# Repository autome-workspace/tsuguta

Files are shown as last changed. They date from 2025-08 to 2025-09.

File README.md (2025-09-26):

# tsugutaのリポジトリ

## KiCadファイル
- MD-AM2837
  - AM2837を使ったシンプルなモタドラ。定格13.5V3.5A(peak 6A)。絶対最大定格15V
- MD-IR2302
  - IR2302を使ったモタドラ。FETにはTOSHIBA製TK7R4A10PL(絶対最大定格100V50A)を使用予定。
- lipo-S.V.-simple-v2
  - li-poバッテリー用の電源電圧監視・保護回路第2版。定格24V35A。各セルの電圧は監視していないため、ほんとは良くない。あくまで簡易版
- my-lib
  - 作る価値のある部品だけ
   
## 【試験運用中】tagについて
- v.x.y
  - x: 0は試作中で動作保証なし、1以降は動く物。1以降では物理的・プログラム的に重大な変更(コネクタ変更、真理値表変更)の場合などに上げる。
  - y: 小さな変更の場合はこちらを上げていく。

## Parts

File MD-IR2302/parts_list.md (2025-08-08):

リファレンス|値|数量|リンク|備考
---|---|---|---|---
C1,C3|10uF|2|[秋月](https://akizukidenshi.com/catalog/g/g113336/)|
C2,C5,C6,C7,C9|0.1uF|5|[秋月](https://akizukidenshi.com/catalog/g/g111384/)|
C4|470uF|1|[秋月](https://akizukidenshi.com/catalog/g/g102719/)|
C8|0.47uF|1|[秋月](https://akizukidenshi.com/catalog/g/g117142/)|
C10,C11|220uF|2|[秋月](https://akizukidenshi.com/catalog/g/g102718/)|実装しない
D1,D2|1N4148|2|[秋月](https://akizukidenshi.com/catalog/g/g100941/)|
J1|XT60メス基板実装用|1|[秋月](https://akizukidenshi.com/catalog/g/g118155/)|
J2|XH3ピン|1|[秋月](https://akizukidenshi.com/catalog/g/g112248/)|
J3,J4|XH2ピン|2|[秋月](https://akizukidenshi.com/catalog/g/g112247/)|実装しない
J5|XT60オス基板実装用|1|[秋月](https://akizukidenshi.com/catalog/g/g118156/)|
LDO1|NJM7805|1|[秋月](https://akizukidenshi.com/catalog/g/g111237/)|
Q1,Q2,Q3,Q4|TK7R4A10PL|4|[秋月](https://akizukidenshi.com/catalog/g/g116488/)|
R1,R2,R3,R4|47kΩ|4|千石地下一階にて入手可能|1608サイズ
R5,R6|910Ω|2|千石地下一階にて入手可能|1608サイズ
R7,R8,R9,R10|4.7Ω|4|千石地下一階にて入手可能|1608サイズ、抵抗ない時はショートでも可
U1,U2|IR2302|2|[秋月](https://akizukidenshi.com/catalog/g/g115656/)|
U3,U4|TLP2361|2|[秋月](https://akizukidenshi.com/catalog/g/g111004/)|

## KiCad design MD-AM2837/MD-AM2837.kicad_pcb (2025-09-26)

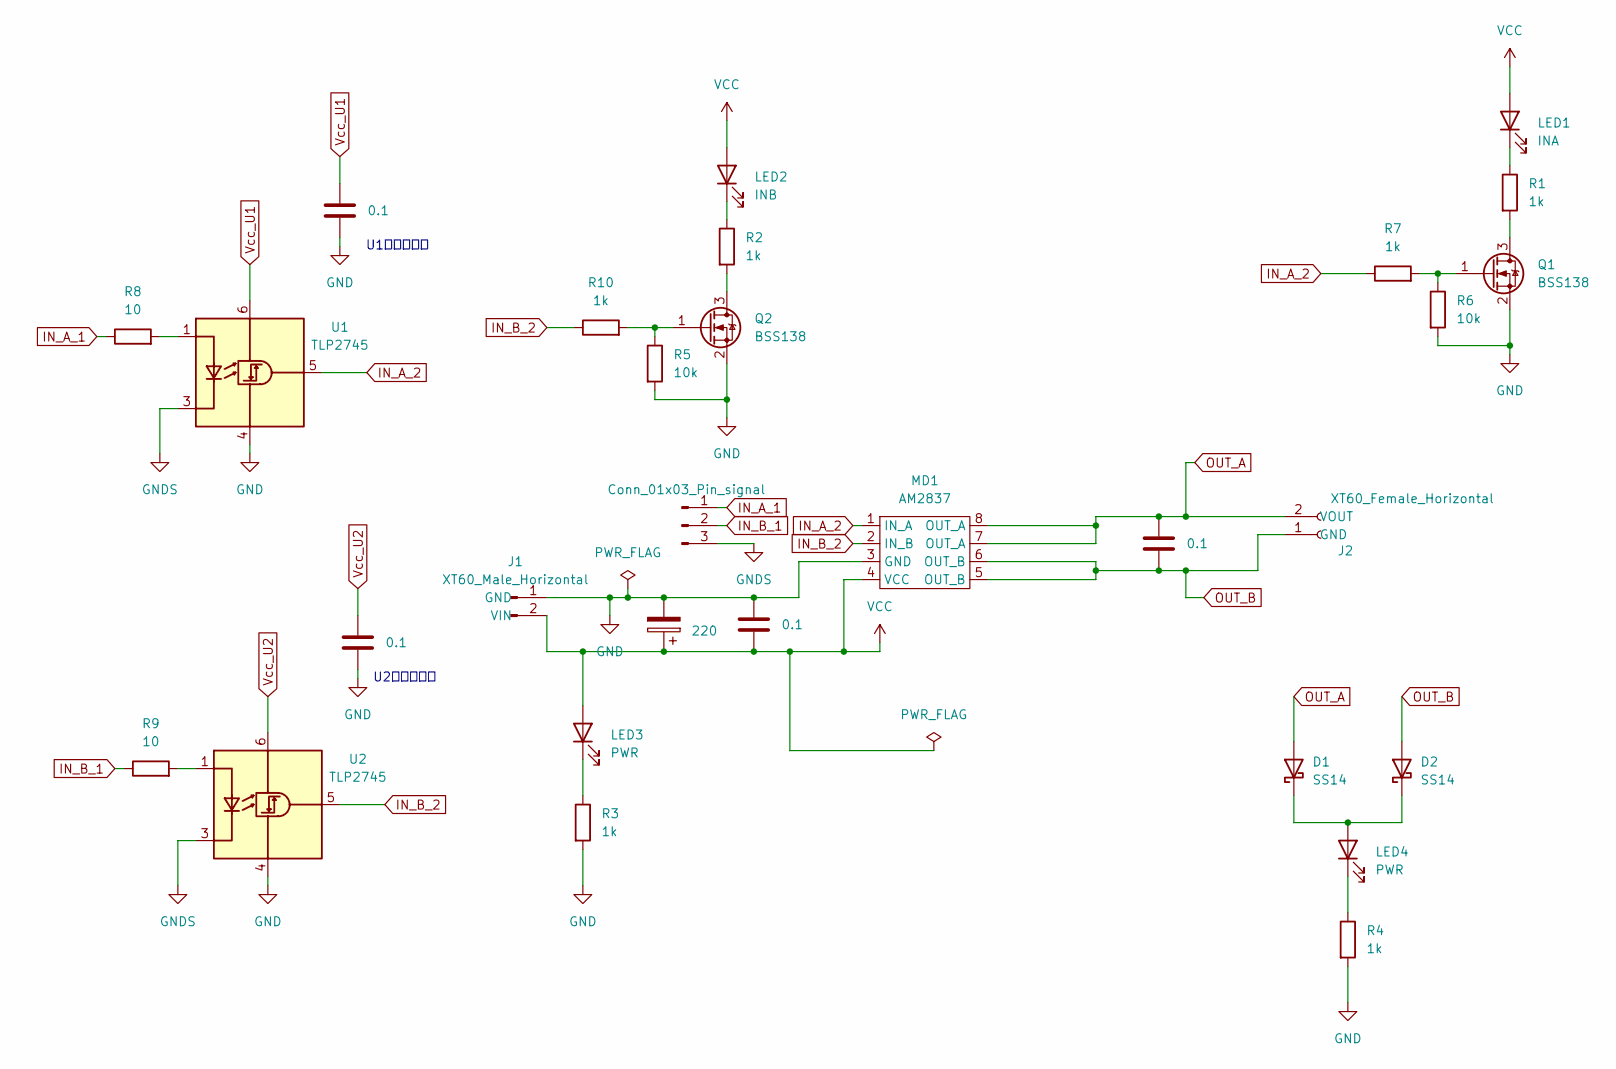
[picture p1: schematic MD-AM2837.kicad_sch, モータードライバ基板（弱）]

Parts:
C1: 220; C_Radial_D8.0mm_H11.5mm_P3.50mm
C2, C3, C4, C5: 0.1; C_0603_1608Metric_Pad1.08x0.95mm_HandSolder
D1, D2: SS14; D_SMA
J1: XT60_Male_Horizontal; AMASS_XT60PW-M_1x02_P7.20mm_Horizontal
J2: XT60_Female_Horizontal; AMASS_XT60PW-F_1x02_P7.20mm_Horizontal
J3: Conn_01x03_Pin_signal; JST_XH_B3B-XH-A_1x03_P2.50mm_Vertical
LED1: INA; LED_0603_1608Metric_Pad1.05x0.95mm_HandSolder
LED2: INB; LED_0603_1608Metric_Pad1.05x0.95mm_HandSolder
LED3, LED4: PWR; LED_0603_1608Metric_Pad1.05x0.95mm_HandSolder
MD1: AM2837; SOP-8_3.9x4.9mm_P1.27mm
Q1, Q2: BSS138; SOT-23
R1, R2, R3, R4, R7, R10: 1k; R_0603_1608Metric_Pad0.98x0.95mm_HandSolder
R5, R6: 10k; R_0603_1608Metric_Pad0.98x0.95mm_HandSolder
R8, R9: 10; R_0603_1608Metric_Pad0.98x0.95mm_HandSolder
U1, U2: TLP2745; SO-6L_10x3.84mm_P1.27mm

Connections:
GND: C1.2, C2.1, C4.2, C5.2, J1.1 (GND), MD1.3 (GND), Q1.2 (S), Q2.2 (S), R3.2, R4.2, R5.2, R6.2, U1.4 (GND), U2.4 (GND)
GNDS: J3.3, U1.3 (K), U2.3 (K)
IN_A_1: J3.1, R8.1
IN_A_2: MD1.1 (IN_A), R7.1, U1.5 (VO)
IN_B_1: J3.2, R9.1
IN_B_2: MD1.2 (IN_B), R10.1, U2.5 (VO)
unnamed: D1.1 (K), D2.1 (K), LED4.2 (A)
unnamed: LED1.1 (K), R1.1
unnamed: LED2.1 (K), R2.1
unnamed: LED3.1 (K), R3.1
unnamed: LED4.1 (K), R4.1
unnamed: Q1.3 (D), R1.2
unnamed: Q1.1 (G), R6.1, R7.2
unnamed: Q2.3 (D), R2.2
unnamed: Q2.1 (G), R5.1, R10.2
unnamed: R8.2, U1.1 (A)
unnamed: R9.2, U2.1 (A)
OUT_A: C3.1, D1.2 (A), J2.2 (VOUT), MD1.7 (OUT_A), MD1.8 (OUT_A)
OUT_B: C3.2, D2.2 (A), J2.1 (GND), MD1.5 (OUT_B), MD1.6 (OUT_B)
VCC: C1.1, C2.2, J1.2 (VIN), LED1.2 (A), LED2.2 (A), LED3.2 (A), MD1.4 (VCC)
Vcc_U1: C4.1, U1.6 (VDD)
Vcc_U2: C5.1, U2.6 (VDD)

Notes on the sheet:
U1に近づける
U2に近づける

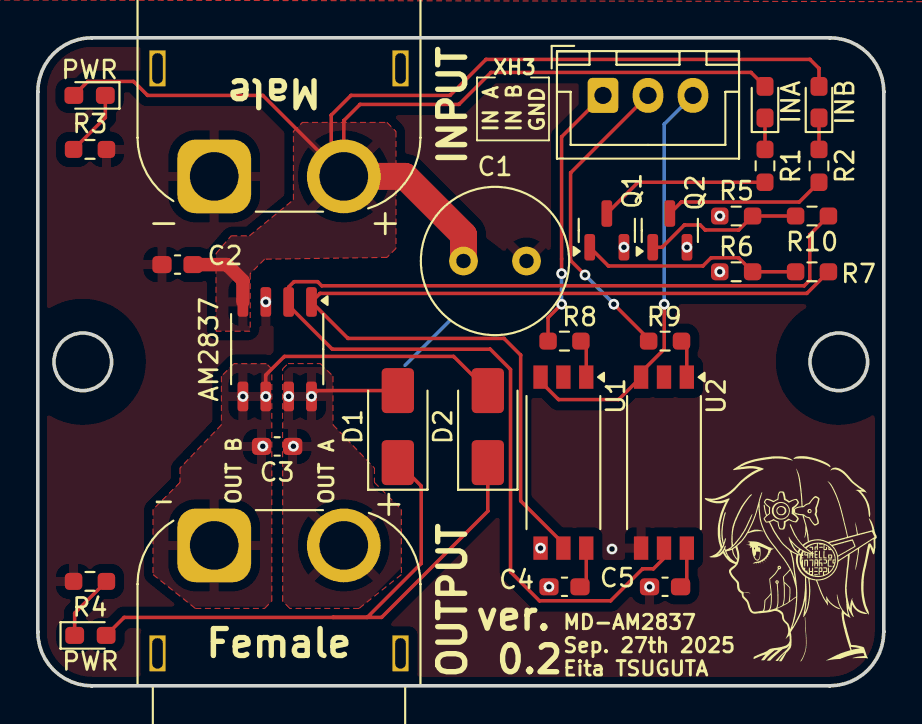
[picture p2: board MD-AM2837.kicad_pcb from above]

Board: 2 copper layers, 47.0 x 36.0 mm, 29 parts (0 on the bottom side), 22 nets.

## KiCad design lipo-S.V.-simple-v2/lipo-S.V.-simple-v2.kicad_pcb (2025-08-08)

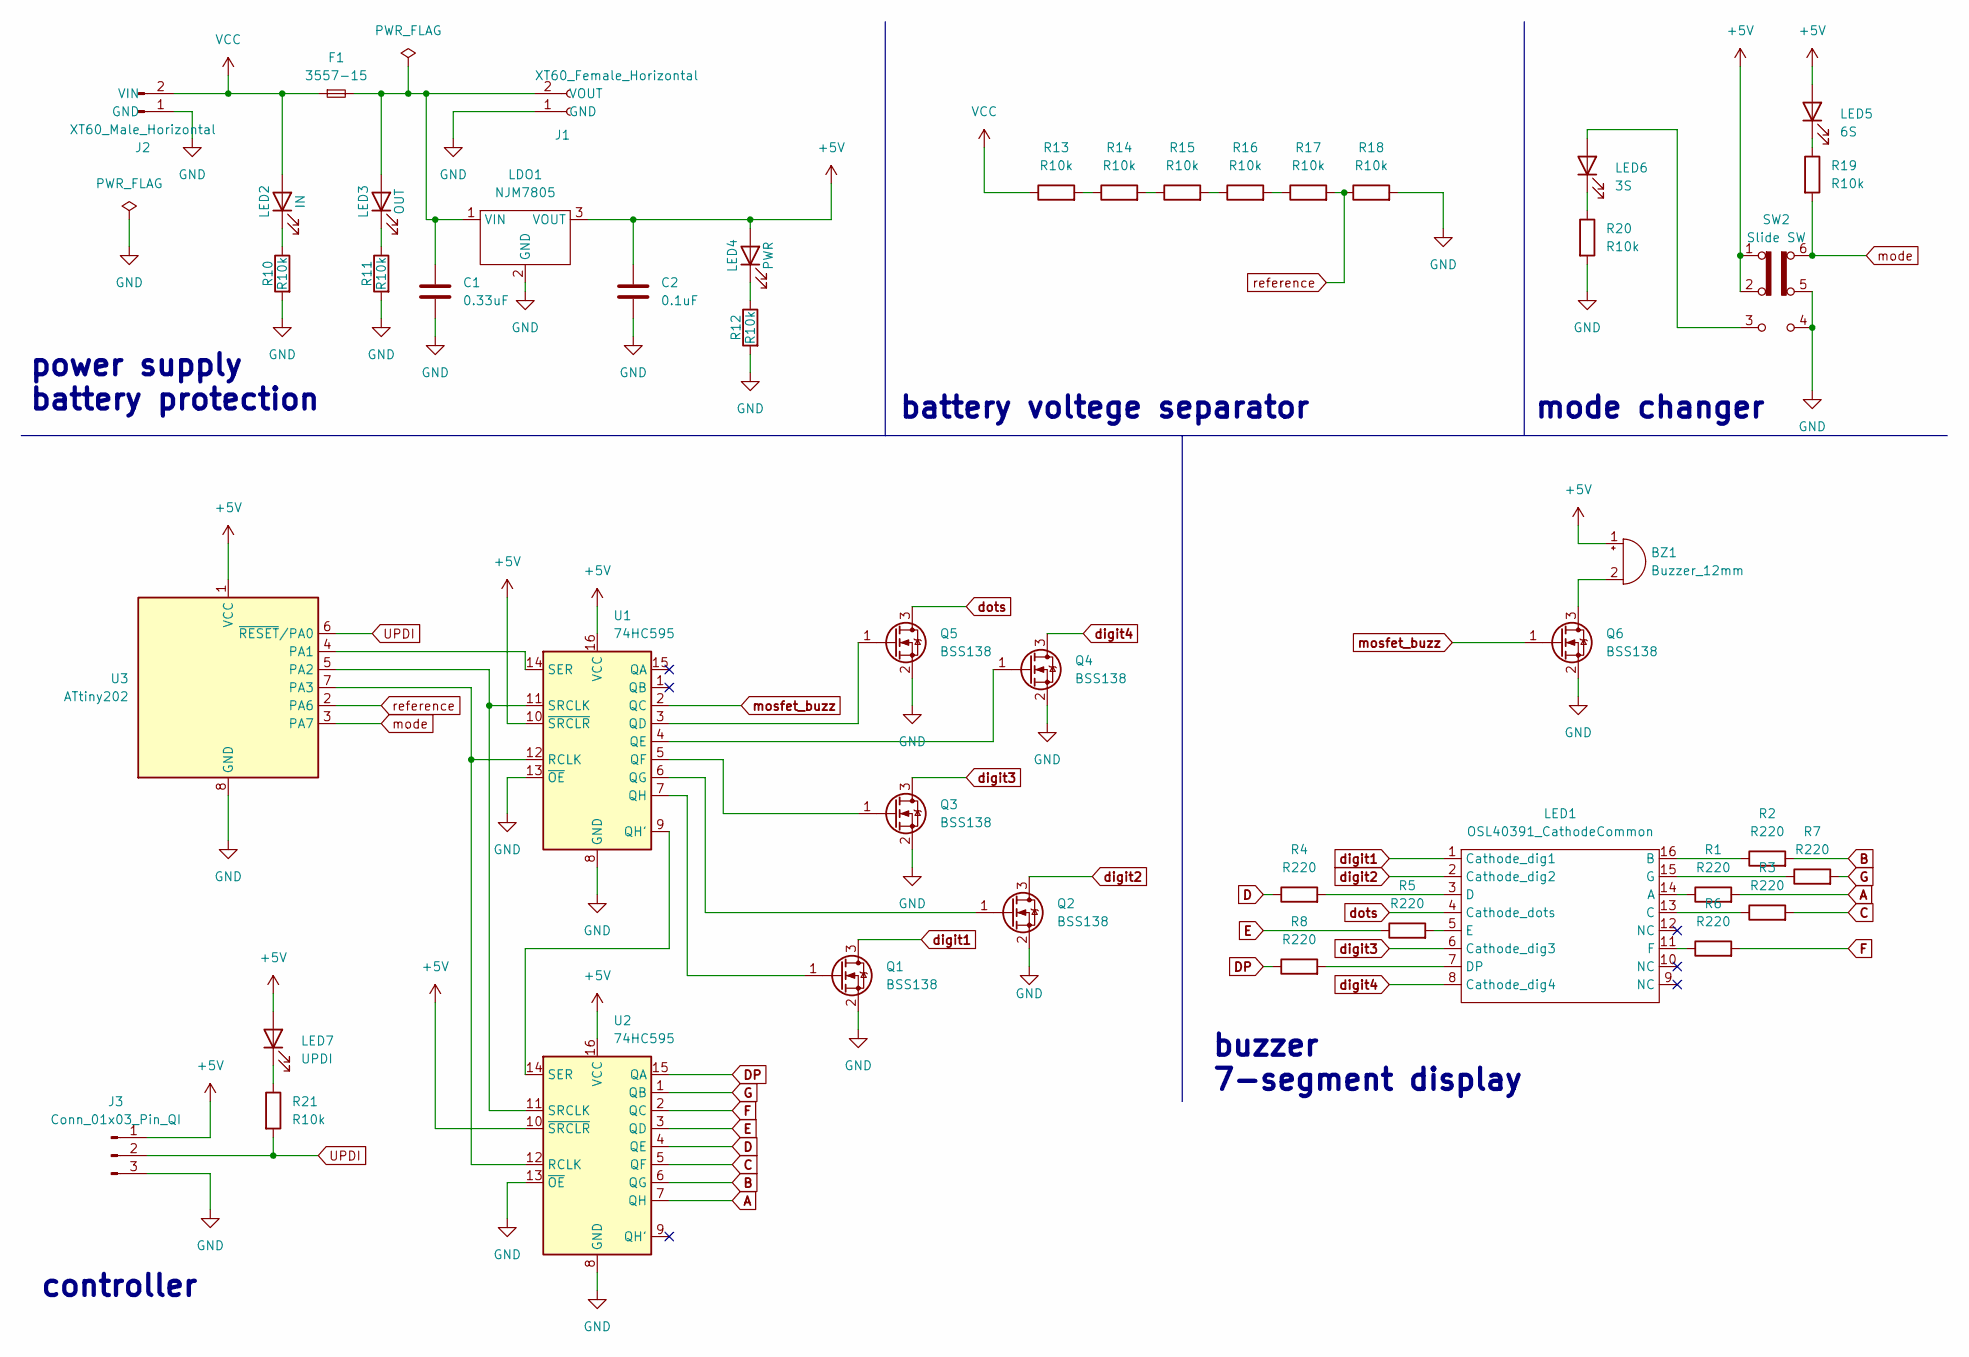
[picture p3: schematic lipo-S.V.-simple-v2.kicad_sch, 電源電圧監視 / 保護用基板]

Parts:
BZ1: Buzzer_12mm; Buzzer_12x9.5RM7.6
C1: 0.33uF; C_0603_1608Metric_Pad1.08x0.95mm_HandSolder
C2: 0.1uF; C_0603_1608Metric_Pad1.08x0.95mm_HandSolder
F1: 3557-15; FuseHolder_3557_15
J1: XT60_Female_Horizontal; AMASS_XT60PW-F_1x02_P7.20mm_Horizontal
J2: XT60_Male_Horizontal; AMASS_XT60PW-M_1x02_P7.20mm_Horizontal
J3: Conn_01x03_Pin_QI; PinHeader_1x03_P2.54mm_Vertical
LDO1: NJM7805; TO-252-2
LED1: OSL40391_CathodeCommon
LED2: IN; LED_0603_1608Metric_Pad1.05x0.95mm_HandSolder
LED3: OUT; LED_0603_1608Metric_Pad1.05x0.95mm_HandSolder
LED4: PWR; LED_0603_1608Metric_Pad1.05x0.95mm_HandSolder
LED5: 6S; LED_0603_1608Metric_Pad1.05x0.95mm_HandSolder
LED6: 3S; LED_0603_1608Metric_Pad1.05x0.95mm_HandSolder
LED7: UPDI; LED_0603_1608Metric_Pad1.05x0.95mm_HandSolder
Q1, Q2, Q3, Q4, Q5, Q6: BSS138; SOT-23
R1, R2, R3, R4, R5, R6, R7, R8: R220; R_0603_1608Metric_Pad0.98x0.95mm_HandSolder
R10, R11, R12, R13, R14, R15, R16, R17, R18, R19, R20, R21: R10k; R_0603_1608Metric_Pad0.98x0.95mm_HandSolder
SW2: Slide SW; SW_CK_JS202011CQN_DPDT_Straight
U1, U2: 74HC595; SOP-16_4.55x10.3mm_P1.27mm
U3: ATtiny202; SOIC-8_3.9x4.9mm_P1.27mm

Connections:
+5V: BZ1.1 (+), C2.1, J3.1, LDO1.3 (VOUT), LED4.2 (A), LED5.2 (A), LED7.2 (A), SW2.1 (A), SW2.2 (B), U1.10 (~SRCLR), U1.16 (VCC), U2.10 (~SRCLR), U2.16 (VCC), U3.1 (VCC)
A: R1.2, U2.7 (QH)
B: R2.2, U2.6 (QG)
C: R3.2, U2.5 (QF)
D: R4.1, U2.4 (QE)
DP: R8.1, U2.15 (QA)
E: R5.1, U2.3 (QD)
F: R6.2, U2.2 (QC)
G: R7.2, U2.1 (QB)
GND: C1.2, C2.2, J1.1 (GND), J2.1 (GND), J3.3, LDO1.2 (GND), Q1.2 (S), Q2.2 (S), Q3.2 (S), Q4.2 (S), Q5.2 (S), Q6.2 (S), R10.2, R11.2, R12.2, R18.2, R20.2, SW2.4 (A), SW2.5 (B), U1.8 (GND), U1.13 (~OE), U2.8 (GND), U2.13 (~OE), U3.8 (GND)
unnamed: BZ1.2 (-), Q6.3 (D)
unnamed: C1.1, F1.2, J1.2 (VOUT), LDO1.1 (VIN), LED3.2 (A)
unnamed: LED1.14 (A), R1.1
unnamed: LED1.16 (B), R2.1
unnamed: LED1.13 (C), R3.1
unnamed: LED1.3 (D), R4.2
unnamed: LED1.7 (DP), R8.2
unnamed: LED1.5 (E), R5.2
unnamed: LED1.11 (F), R6.1
unnamed: LED1.15 (G), R7.1
unnamed: LED2.1 (K), R10.1
unnamed: LED3.1 (K), R11.1
unnamed: LED4.1 (K), R12.1
unnamed: LED5.1 (K), R19.1
unnamed: LED6.2 (A), SW2.3 (C)
unnamed: LED6.1 (K), R20.1
unnamed: LED7.1 (K), R21.1
unnamed: Q1.1 (G), U1.7 (QH)
unnamed: Q2.1 (G), U1.6 (QG)
unnamed: Q3.1 (G), U1.5 (QF)
unnamed: Q4.1 (G), U1.4 (QE)
unnamed: Q5.1 (G), U1.3 (QD)
unnamed: R13.2, R14.1
unnamed: R14.2, R15.1
unnamed: R15.2, R16.1
unnamed: R16.2, R17.1
unnamed: U1.9 (QH'), U2.14 (SER)
unnamed: U1.12 (RCLK), U2.12 (RCLK), U3.7 (PA3)
unnamed: U1.14 (SER), U3.4 (PA1)
unnamed: U1.11 (SRCLK), U2.11 (SRCLK), U3.5 (PA2)
UPDI: J3.2, R21.2, U3.6 (~RESET/PA0)
VCC: F1.1, J2.2 (VIN), LED2.2 (A), R13.1
digit1: LED1.1 (Cathode_dig1), Q1.3 (D)
digit2: LED1.2 (Cathode_dig2), Q2.3 (D)
digit3: LED1.6 (Cathode_dig3), Q3.3 (D)
digit4: LED1.8 (Cathode_dig4), Q4.3 (D)
dots: LED1.4 (Cathode_dots), Q5.3 (D)
mode: R19.2, SW2.6 (C), U3.3 (PA7)
mosfet_buzz: Q6.1 (G), U1.2 (QC)
reference: R17.2, R18.1, U3.2 (PA6)

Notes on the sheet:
mode changer
controller
battery voltege separator
buzzer 7-segment display
power supply battery protection

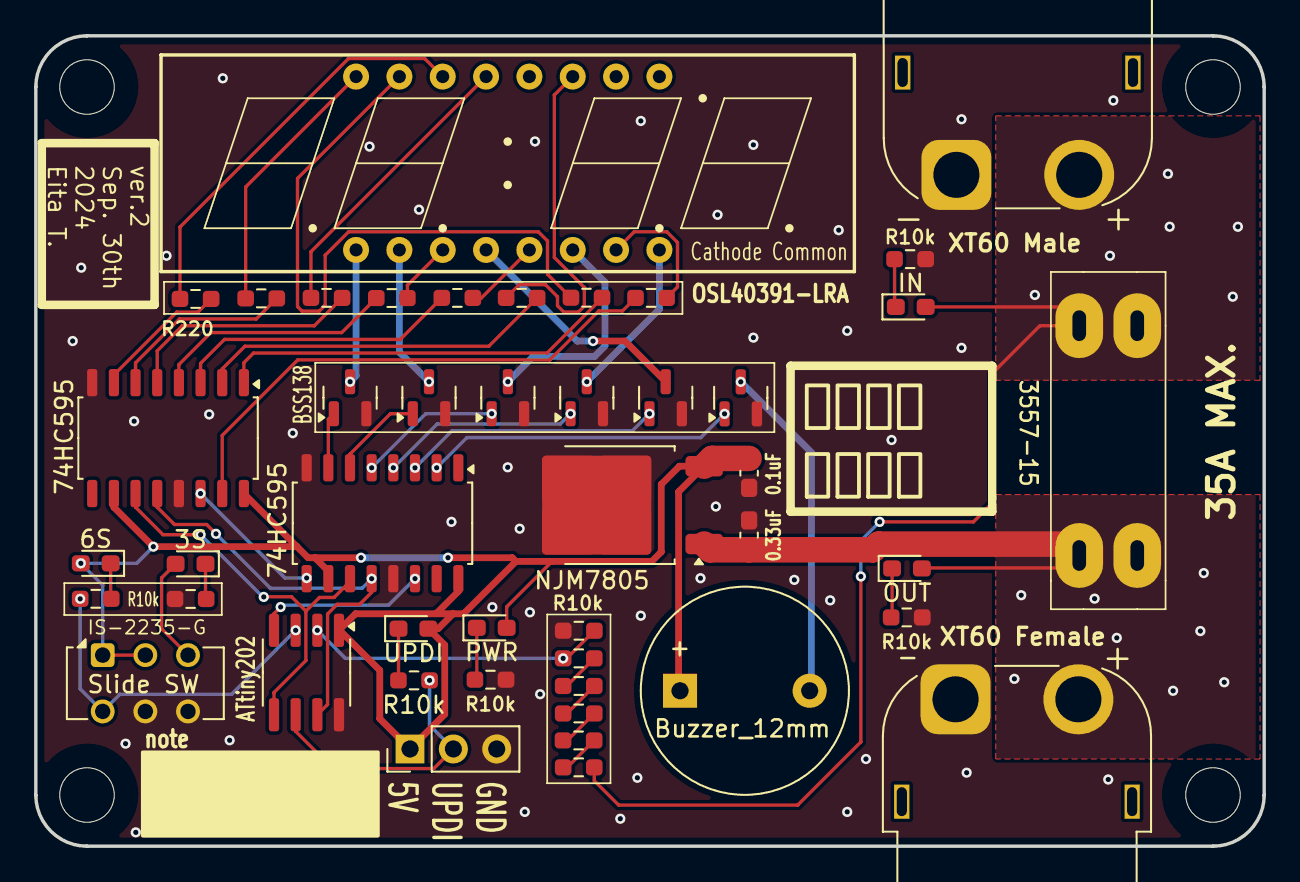
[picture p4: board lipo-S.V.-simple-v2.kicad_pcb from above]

Board: 2 copper layers, 72.0 x 47.5 mm, 45 parts (0 on the bottom side), 50 nets.

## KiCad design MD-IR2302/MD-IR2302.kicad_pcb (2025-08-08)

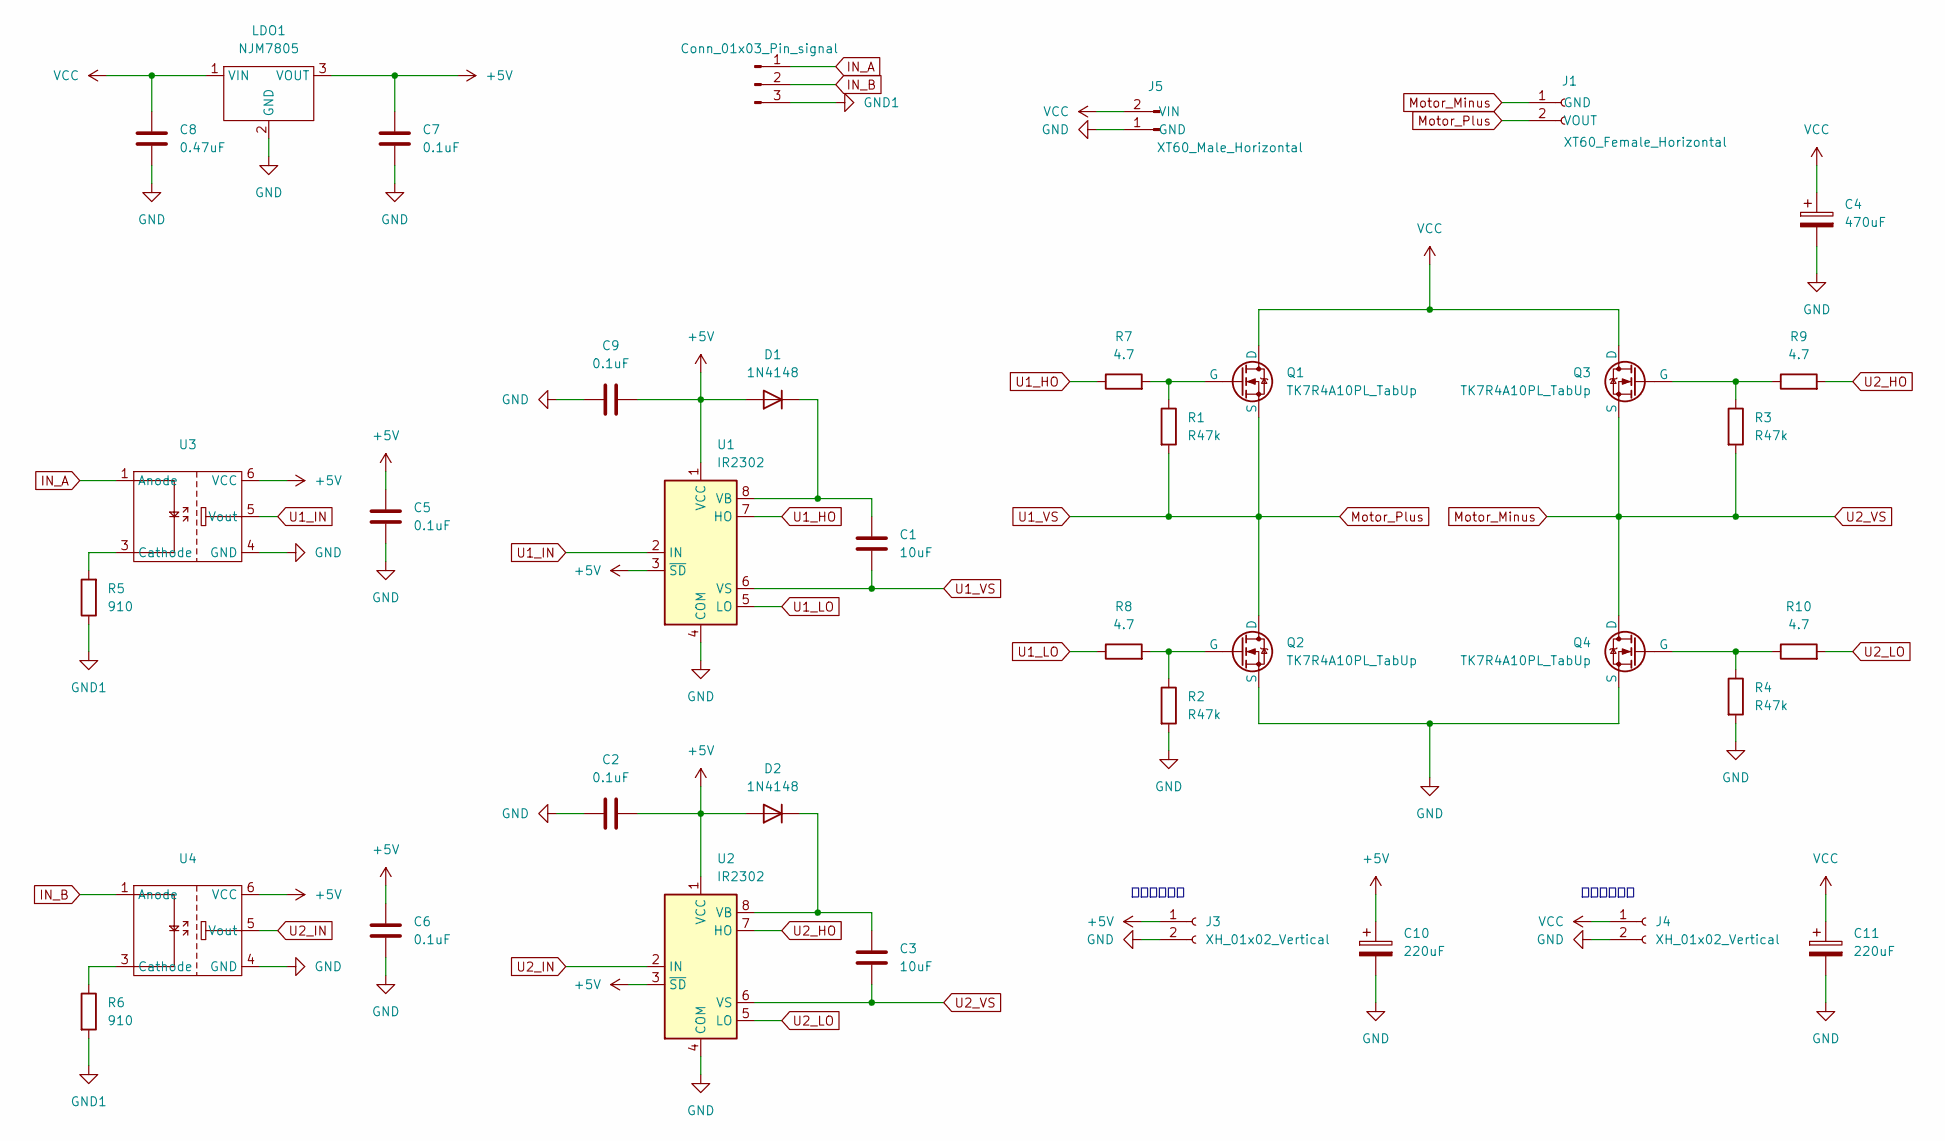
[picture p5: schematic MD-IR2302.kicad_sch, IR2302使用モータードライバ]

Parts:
C1, C3: 10uF; C_0805_2012Metric_Pad1.18x1.45mm_HandSolder
C2, C5, C6, C7, C9: 0.1uF; C_0805_2012Metric_Pad1.18x1.45mm_HandSolder
C4: 470uF; CP_Radial_D10.0mm_P5.00mm
C8: 0.47uF; C_0805_2012Metric_Pad1.18x1.45mm_HandSolder
C10, C11: 220uF; CP_Radial_D8.0mm_P3.50mm
D1, D2: 1N4148; D_DO-35_SOD27_P7.62mm_Horizontal
J1: XT60_Female_Horizontal; AMASS_XT60PW-F_1x02_P7.20mm_Horizontal
J2: Conn_01x03_Pin_signal; JST_XH_B3B-XH-A_1x03_P2.50mm_Vertical
J3, J4: XH_01x02_Vertical; JST_XH_B2B-XH-A_1x02_P2.50mm_Vertical
J5: XT60_Male_Horizontal; AMASS_XT60PW-M_1x02_P7.20mm_Horizontal
LDO1: NJM7805; TO-252-2
Q1, Q2, Q3, Q4: TK7R4A10PL_TabUp; TO-220-3_Horizontal_TabUp
R1, R2, R3, R4: R47k; R_0603_1608Metric_Pad0.98x0.95mm_HandSolder
R5, R6: 910; R_0603_1608Metric_Pad0.98x0.95mm_HandSolder
R7, R8, R9, R10: 4.7; R_0603_1608Metric_Pad0.98x0.95mm_HandSolder
U1, U2: IR2302; SOP-8_3.9x4.9mm_P1.27mm
U3, U4: MFSOP6-5_4.4x3.6mm_P1.27mm

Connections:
+5V: C2.2, C5.2, C6.2, C7.2, C9.2, C10.1, D1.2 (A), D2.2 (A), J3.1, LDO1.3 (VOUT), U1.1 (VCC), U1.3 (~SD), U2.1 (VCC), U2.3 (~SD), U3.6 (VCC), U4.6 (VCC)
GND: C2.1, C4.2, C5.1, C6.1, C7.1, C8.2, C9.1, C10.2, C11.2, J3.2, J4.2, J5.1 (GND), LDO1.2 (GND), Q2.3 (S), Q4.3 (S), R2.2, R4.2, U1.4 (COM), U2.4 (COM), U3.4 (GND), U4.4 (GND)
GND1: J2.3, R5.1, R6.2
IN_A: J2.1, U3.1 (Anode)
IN_B: J2.2, U4.1 (Anode)
Motor_Minus: C3.2, J1.1 (GND), Q3.3 (S), Q4.1 (D), R3.2, U2.6 (VS)
Motor_Plus: C1.2, J1.2 (VOUT), Q1.3 (S), Q2.1 (D), R1.2, U1.6 (VS)
unnamed: C1.1, D1.1 (K), U1.8 (VB)
unnamed: C3.1, D2.1 (K), U2.8 (VB)
unnamed: Q1.2 (G), R1.1, R7.2
unnamed: Q2.2 (G), R2.1, R8.2
unnamed: Q3.2 (G), R3.1, R9.1
unnamed: Q4.2 (G), R4.1, R10.1
unnamed: R5.2, U3.3 (Cathode)
unnamed: R6.1, U4.3 (Cathode)
U1_HO: R7.1, U1.7 (HO)
U1_IN: U1.2 (IN), U3.5 (Vout)
U1_LO: R8.1, U1.5 (LO)
U2_HO: R9.2, U2.7 (HO)
U2_IN: U2.2 (IN), U4.5 (Vout)
U2_LO: R10.2, U2.5 (LO)
VCC: C4.1, C8.1, C11.1, J4.1, J5.2 (VIN), LDO1.1 (VIN), Q1.1 (D), Q3.1 (D)

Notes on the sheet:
ファン用電源

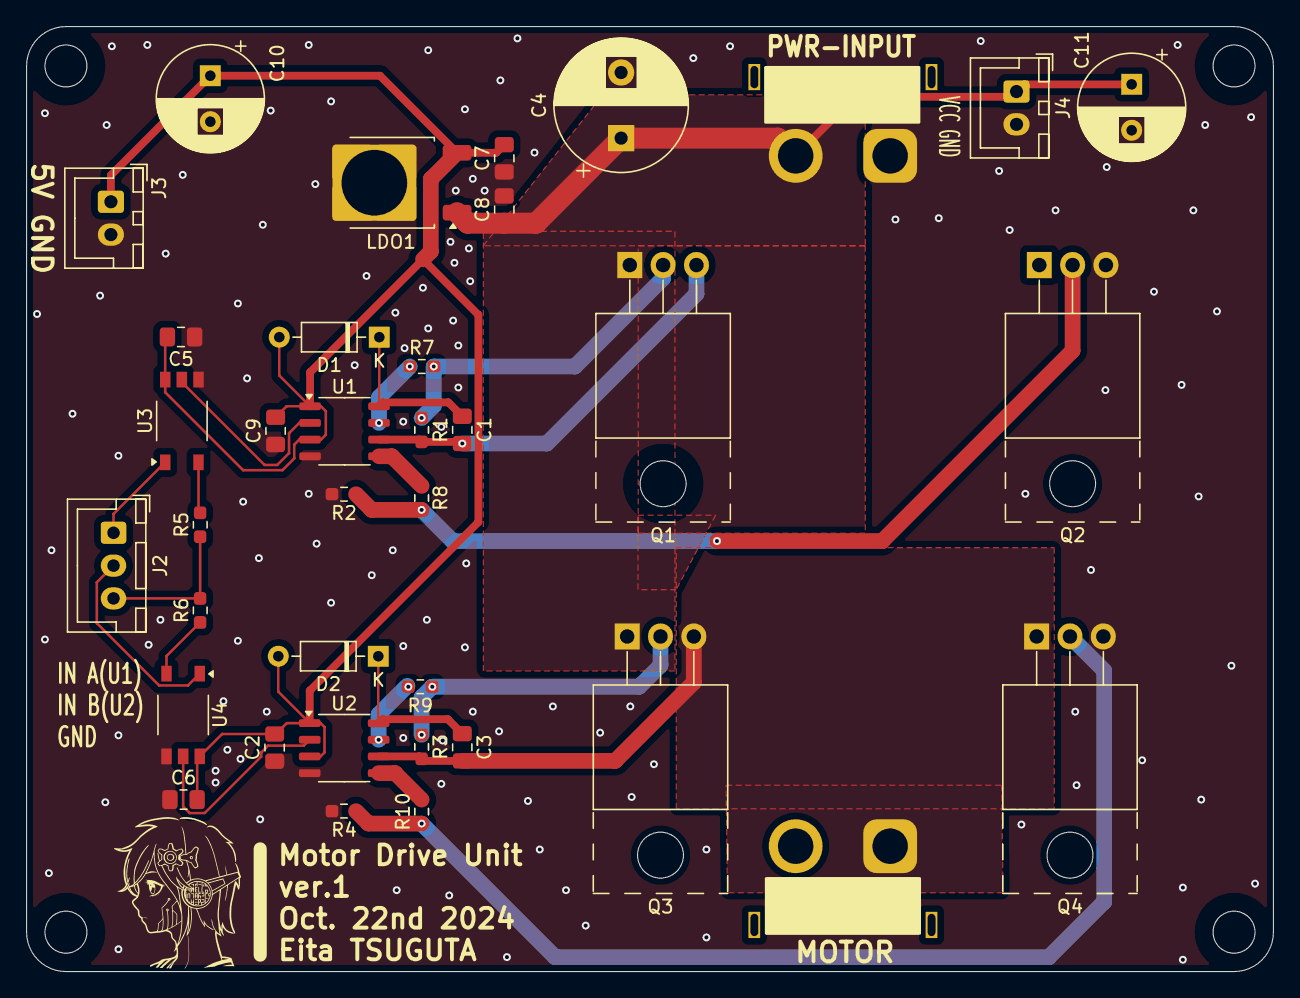
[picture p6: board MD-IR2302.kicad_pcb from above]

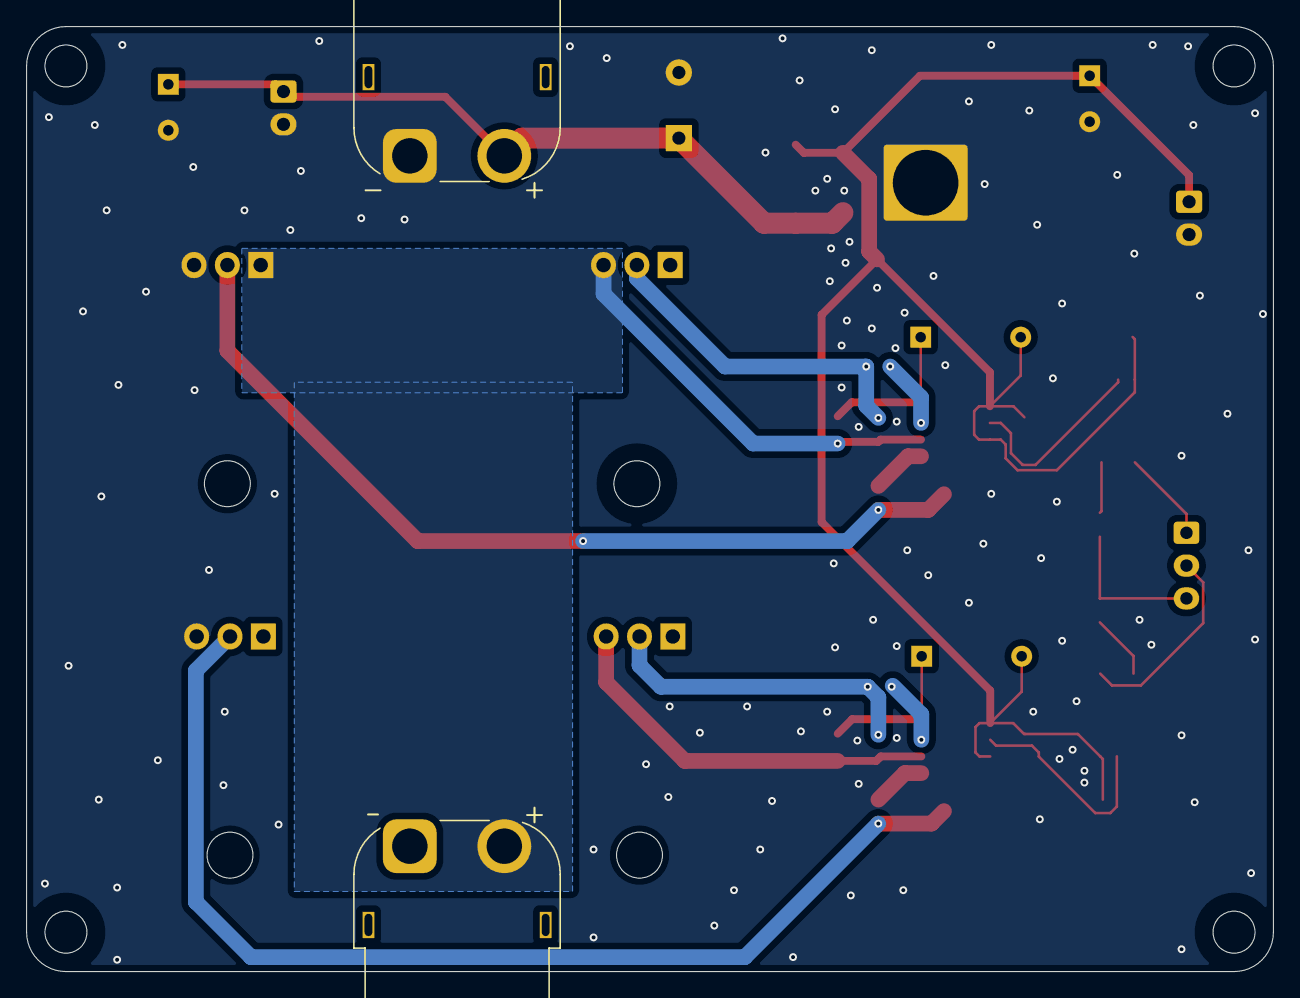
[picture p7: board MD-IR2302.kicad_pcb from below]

Board: 2 copper layers, 95.0 x 72.0 mm, 37 parts (2 on the bottom side), 22 nets.

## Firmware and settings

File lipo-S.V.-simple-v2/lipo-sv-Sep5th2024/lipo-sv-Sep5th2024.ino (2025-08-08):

#include <avr/pgmspace.h>

const int SER = A1;
const int CLK = A2;
const int LATCH = A3;
const int REFERENCE = A6;
const int MODE = A7;

byte b1 = 0b00000000;
byte b2 = 0b00000000;
// 以下b1b2兼用
const byte null = 0b00000000;
// 以下b2用
const byte buzz = 0b00100000;
// 以下b1用
const byte num0 PROGMEM = 0b00111111;
const byte num1 PROGMEM = 0b00000110;
const byte num2 PROGMEM = 0b01011011;
const byte num3 PROGMEM = 0b01001111;
const byte num4 PROGMEM = 0b01100110;
const byte num5 PROGMEM = 0b01101101;
const byte num6 PROGMEM = 0b01111101;
const byte num7 PROGMEM = 0b00000111;
const byte num8 PROGMEM = 0b01111111;
const byte num9 PROGMEM = 0b01101111;
const byte dot  PROGMEM = 0b10000000;
const byte C    PROGMEM = 0b00111001;
const byte E    PROGMEM = 0b01111001;
const byte L    PROGMEM = 0b00111000;
const byte LEDA PROGMEM = 0b00000001;
const byte LEDB PROGMEM = 0b00000010;
const byte LEDC PROGMEM = 0b00000100;
const byte LEDD PROGMEM = 0b00001000;
const byte LEDE PROGMEM = 0b00010000;
const byte LEDF PROGMEM = 0b00100000;
const byte LEDG PROGMEM = 0b01000000;

const byte cell3[]        = {num3, C, E, L+dot};
const byte cell2[]        = {num2, C, E, L+dot};
const byte num[]          = {num0, num1, num2, num3, num4, num5, num6, num7, num8, num9};
const byte blinkPattern[] = {LEDG, LEDB, LEDA, LEDF, LEDE, LEDD, LEDC, dot};

const int attentionVoltageLevel = 3700; // 1Sあたり。単位はmV
const int warningVoltageLevel = 3500; //1Sあたり。単位はmV
const int gain = 1027; //測定電圧の誤差修正用。算出方法: テスターでの測定値 / ゲイン無しでの表示値 * 1000
int cellAmount = 0;
int attentionFlg = 0;
int warningFlg = 0;
int displayCnt = 4;
int displayOffCnt = 0;

void setup() {
  pinMode(SER, OUTPUT);
  pinMode(CLK, OUTPUT);
  pinMode(LATCH, OUTPUT);
  pinMode(MODE, INPUT);

  blinkInit();
}

void loop() {
  int batteryVoltage = getVoltage();
  for (int i = 0; i < 500; i++) {
    if (attentionFlg == 1) {
      batteryVoltage = getVoltage();
    }
    cellModeDetector();
    displayVoltage(batteryVoltage);
    checkVoltage(batteryVoltage);
  }
}

void shiftOutData() {
  digitalWrite(LATCH, 0);
  shiftOut(SER, CLK, LSBFIRST, b1);
  shiftOut(SER, CLK, LSBFIRST, b2);
  digitalWrite(LATCH, 1);
}

void blinkInit() {
  b2 = null;
  for (int i = 0; i < 4; i++) {
    b1 = null;
    shiftOutData();
    b2 <<= 1;
  }
  delay(500);
  b2 = 0b00000001;
  for (int i = 0; i < 8; i++) {
    for (int j = 0; j < 1500; j++) {
      b1 = blinkPattern[i];
      shiftOutData();
      b2 <<= 1;
      if (b2 == 0b00010000) {
        b2 = 0b00000001;
      }
    }
  }
  for (int i; i < 2; i++){
    b2 = buzz;
    shiftOutData();
    delay(10);
    b2 = null;
    shiftOutData();
    delay(490);
  }
}

void checkVoltage(int batteryVoltage) {
  int cellVoltage = batteryVoltage / cellAmount;
  if (cellVoltage < attentionVoltageLevel) {
    attentionFlg = 1;
  }else {
    attentionFlg = 0;
  }
  if (cellVoltage < warningVoltageLevel) {
    warningFlg = 1;
  }else {
    warningFlg = 0;
  }
}

void displayOff() {
  b2 = 0b00000001;
  for (int i = 0; i < displayOffCnt; i++) {
    b1 = null;
    shiftOutData();
    b2 <<= 1;
    if (b2 == 0b00010000) {
      b2 = 0b00000001;
    }
  }
}

int getVoltage() {
  long batteryVoltage = (long)analogRead(REFERENCE) * 5 * 6 * 1000 / 1023;
  batteryVoltage = (long)batteryVoltage * gain / 1000;
  return batteryVoltage;
}

void displayVoltage(int batteryVoltage) {
  int voltageDigit[4];
  voltageDigit[0] = batteryVoltage / 10000;
  voltageDigit[1] = batteryVoltage % 10000 / 1000;
  voltageDigit[2] = batteryVoltage % 10000 % 1000 / 100;
  voltageDigit[3] = batteryVoltage % 10000 % 1000 % 100 / 10;
  if (attentionFlg == 1) {
    displayCnt = 3000;
    displayOffCnt = 2000;
  }else {
    displayCnt = 4;
  }
  b2 = 0b00000001;
  for (int i = 0; i < displayCnt; i++) {
    b1 = num[voltageDigit[i%4]];
    if (i%4 == 1) {
      b1 += dot;
    }
    if (i%4 == 0 && voltageDigit[0] == 0) {
      b1 = null;
    }
    if (warningFlg == 1) {
      b2 += buzz;
    }
    shiftOutData();
    if (warningFlg == 1) {
      b2 -= buzz;
    }
    b2 <<= 1;
    if (b2 == 0b00010000) {
      b2 = 0b00000001;
    }
  }
  if (attentionFlg == 1) {
   displayOff();
  }
}

void cellModeDetector() {
  int modeDisplayCnt = 7000;
  if (digitalRead(MODE) == 1 && cellAmount != 3) {
    b2 = 0b00000001;
    for (int i = 0; i < modeDisplayCnt; i++) {
      b1 = cell3[i%4];
      shiftOutData();
      b2 <<= 1;
      if (b2 == 0b00010000) {
        b2 = 0b00000001;
      }
    }
    cellAmount = 3;
  }else if (digitalRead(MODE) == 0 && cellAmount != 2) {
    b2 = 0b00000001;
    for (int i = 0; i < modeDisplayCnt; i++) {
      b1 = cell2[i%4];
      shiftOutData();
      b2 <<= 1;
      if (b2 == 0b00010000) {
        b2 = 0b00000001;
      }
    }
    cellAmount = 2;
  }
}

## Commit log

2025-08-08 nhkrcでのファイルを移動
    [MD-AM2837.kicad_pcb, MD-AM2837.kicad_sch, MD-IR2302.kicad_pcb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]
2025-09-07 Fix formatting of lipo-S.V.-simple-v2 entry in README
2025-09-07 Fix voltage rating description in README.md
2025-09-26 フォトカプラ追加中
    [MD-AM2837.kicad_pcb, MD-AM2837.kicad_sch]
2025-09-26 ライブラリの項目追加。ライブラリ自体は未作成。
2025-09-26 v0.2作成
    [MD-AM2837.kicad_pcb, MD-AM2837.kicad_sch]
